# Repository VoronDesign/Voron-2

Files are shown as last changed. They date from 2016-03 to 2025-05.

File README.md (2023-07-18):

# Voron 2.4
**[CLICK HERE TO DOWNLOAD](https://voron.zip/done/V2.zip)**

The above link includes the stealthburner toolhead files which are compatible with several of the printers in the Voron lineup. 
To keep things organized, StealthBurner’s files are maintained separately. 
the Stealthburner Repository can be browsed by clicking [HERE](https://github.com/VoronDesign/Voron-Stealthburner)

Image of Voron 2.4

The official release of the Voron 2.4 3d printer.  You can find the BOM in the configurator located at the [Voron Design]( http://vorondesign.com/voron2.4) website.

Voron Logo

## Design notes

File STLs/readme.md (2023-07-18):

you can download the entire STL folder by clicking [HERE](https://download-directory.github.io/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)

This printer uses the StealthBurner toolhead, which is compatible with several of the printers in the Voron lineup. 
To keep things organized, StealthBurner’s files are maintained separately. 
the Stealthburner STL's can be downloaded by clicking [HERE](https://download-directory.github.io/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)

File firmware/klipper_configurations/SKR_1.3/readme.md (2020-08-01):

<B>VORON V2.4 SKR 1.3 Config</B>

This config file is for using two BigTreeTech SKR 1.3 boards on the Voron V2.4. For additional reference material, please reference BigTreeTech's Github page:

https://github.com/bigtreetech/BIGTREETECH-SKR-V1.3/tree/master/BTT%20SKR%20V1.3

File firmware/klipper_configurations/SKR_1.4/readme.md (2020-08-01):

<B>VORON V2.4 SKR 1.4 Config</B>

This config file is for using two BigTreeTech SKR 1.4 boards on the Voron V2.4. For additional reference material, please reference BigTreeTech's Github page:

https://github.com/bigtreetech/BIGTREETECH-SKR-V1.3/tree/master/BTT%20SKR%20V1.4

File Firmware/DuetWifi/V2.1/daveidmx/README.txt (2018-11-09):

Hello, and welcome to my configuration!

If you're new here:

1) This configuration works for my printer. Don't assume it'll work for yours out-of-the-box. Know and understand things before running them blindly.

2) The Duet Getting Started wiki is your friend:
    https://duet3d.dozuki.com/c/Getting_Started
    https://duet3d.dozuki.com/Wiki/Step_by_step_guide

If you want to base your configuration off of mine, here are some files you'll want to edit right away:

*  All settings in config.g.
*  All other files as marked to *ADJUST*:
**  /macros/drive/*.g for drive current and physics
***  "fullcurrent" files are used for normal printing.
***  "downcurrent" files are used for slow homing moves to reduce the impact of crash damage.
     You can opt out of the "downcurrent" profiles by uncommenting a couple lines as descibed in those files.
**  /macros/filament/do_moves_for_*.g for bowden length
**  /macros/heating/toolhead_*.g for your tool heater parameters.
***  NOTE: If you add or rename the profile scripts, also update the script name inside the script itself. This is to support recovering the selection across reboots to make it easy to switch toolheads.
**  /macros/homing/scripts/probe_zlevel.g for the leveling probe points
**  /macros/homing/scripts/probe_x.g for the X dimension
**  /macros/homing/scripts/probe_y.g for the Y dimension
**  /macros/moveto/*.g based on your dimensions
**  /macros/retraction/*.g for your retraction settings
***  NOTE: If you add or rename the profile scripts, also update the script name inside the script itself. This is to support recovering the selection across reboots to make it easy to switch toolheads and retraction profiles.
**  /macros/zprobe/use_i*.g for your inductive probe pins
**  /macros/zprobe/use_m*.g for your mechanical switch pins, and to tune Z-height
***  NOTE: /macros/zprobe/use_mslow.g is the only place you need to tune your Z-height.

Bonus files for the test scripts:
**  /macros/testing/belting/scripts/xy_point_*.g based on your bed dimensions
**  /macros/testing/belting/scripts/z_movecycle_1.g for your Z dimension
**  /macros/drive/*_torture.g

Changes:

* Default probe connectors have changed. The inductive probe has been moved from E0 to Zprobe to free up E0 for a filament detector.
* Added bindings for filament sensors. (Disabled by default.)
* Added bindings for chamber fan (enabled by default) and chamber thermistor and lights (disbled by default).
* Changed drive parameters for V2.1.
* Changed some other default settings to better match spec.

* Fix some fan and temp bugs in the /macros/heating/preheat_*.g scripts.
* Fix filament sensor configuration. (It wasn't turned on!)
* Make toolhead heater and firmware retraction profile selections sticky across reboots to support changing toolheads.
* Add retraction profiles for Volcano.
* Increased motor default idle timeout to 24 hours.

* IMPORTANT: Changed origin coordinates to be at bed center.
* Move toolhead thermistor parameters to the heating/toolhead_* scripts, because they change when you swap toolheads.
* Turn off extruder in print_end.g
* Set the tool to standby temperature (via deselection) when pausing.
* Added a heatbreak thermistor setting.
* Add calibrate_mswitch.g script to help calibrate the mechanical Z offset.
* Add coarse_level.g script to level the gantry for when the default dive height is too small.

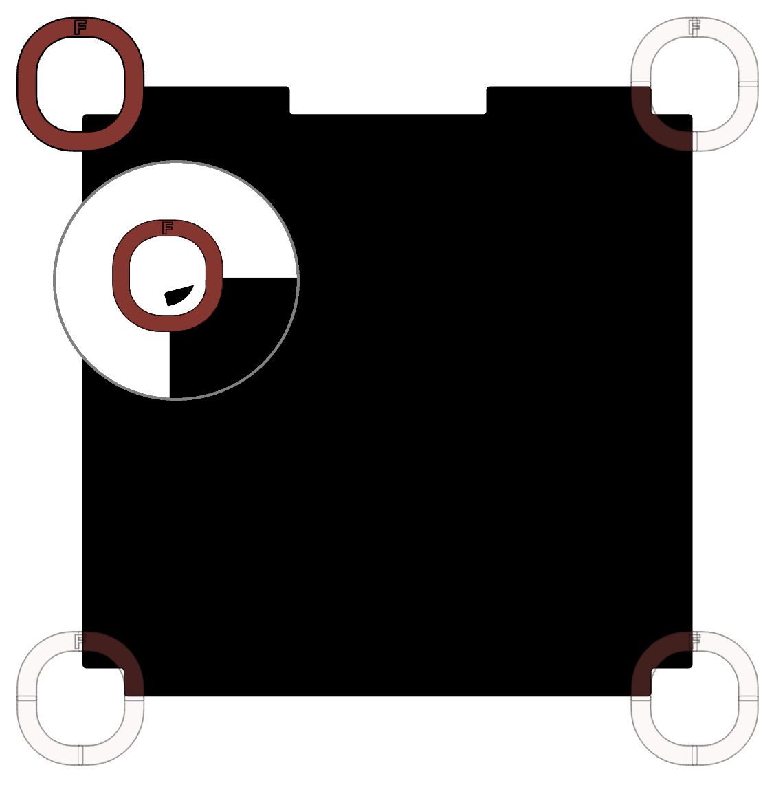
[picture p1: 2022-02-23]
STLs/Tools/bottom_panel_modification.png

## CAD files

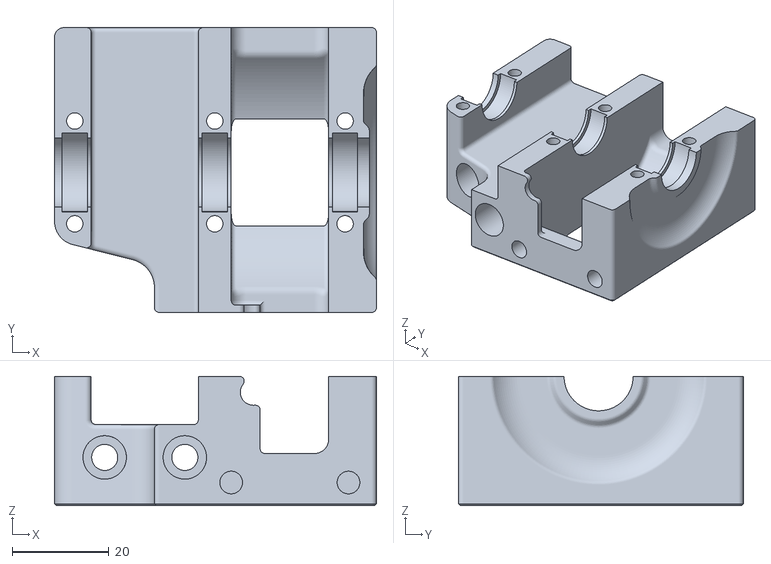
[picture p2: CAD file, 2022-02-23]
STLs/Z_Drive/z_drive_main_b_x2.stl
66.7 x 59.0 x 26.8

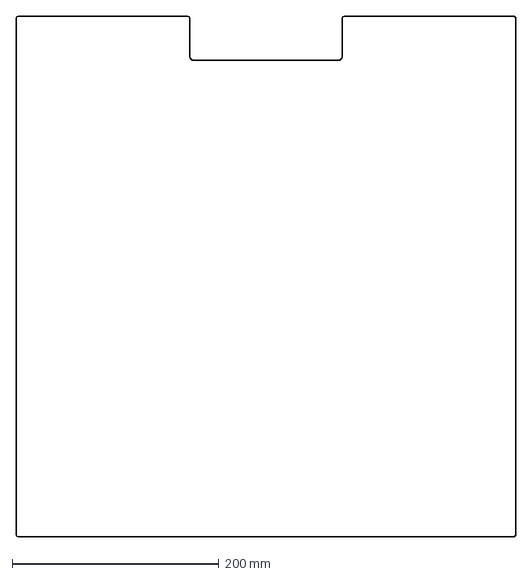
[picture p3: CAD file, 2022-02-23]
Drawing_DXFs/Panels/350_Back_Panel.DXF
483.0 x 503.0 mm

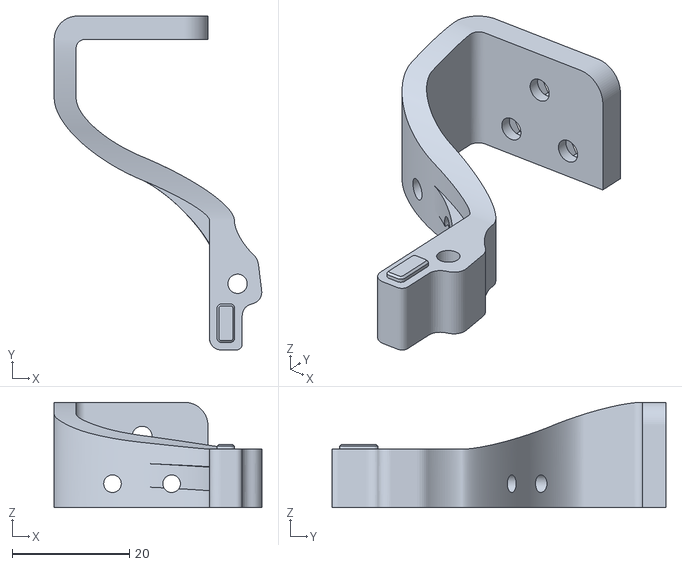
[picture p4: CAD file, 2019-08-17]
mods/warriorofwire/openbuilds_drag_chain_2.1/x_carriage_dragchain_anchorpoint.stl
35.4 x 57.0 x 18.0

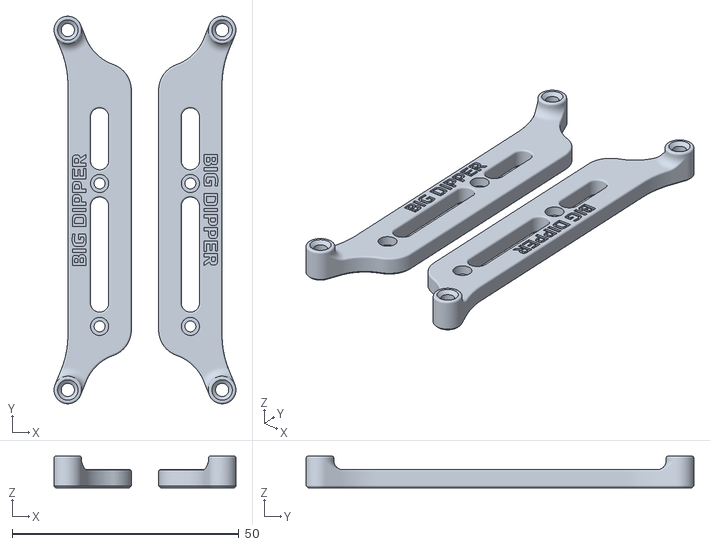
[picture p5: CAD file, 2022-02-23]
STLs/Electronics_Bay/Controller_Mounts/BIGDIPPER_bracket_set.stl
40.1 x 85.4 x 7.00

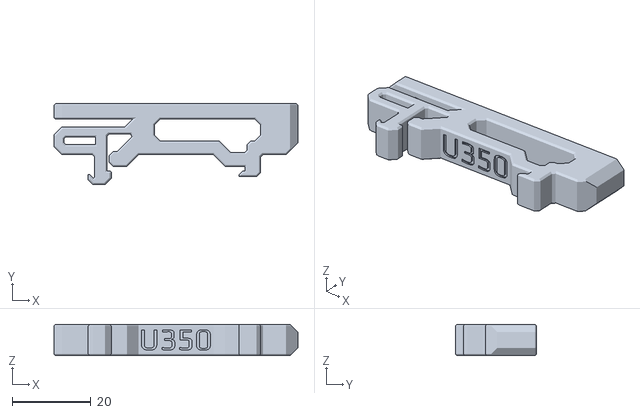
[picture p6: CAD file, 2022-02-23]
STLs/Electronics_Bay/Other_PS_Mounts/UHP_350_Mount_x2.stl
62.0 x 20.6 x 8.00

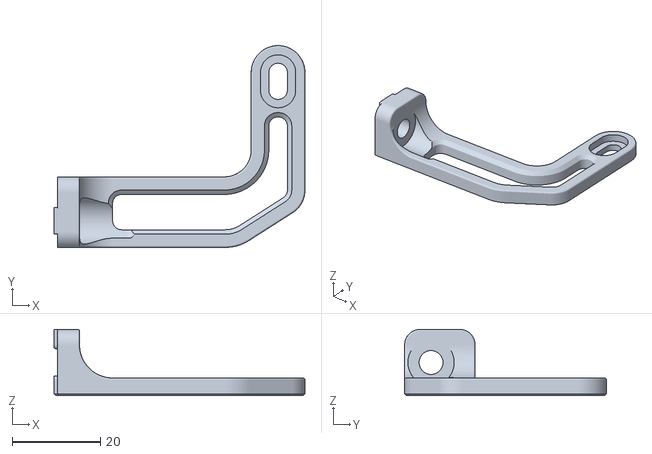
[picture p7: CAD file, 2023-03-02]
STLs/Electronics_Bay/PSU_stabilizer_50mm.stl
56.9 x 45.7 x 15.0

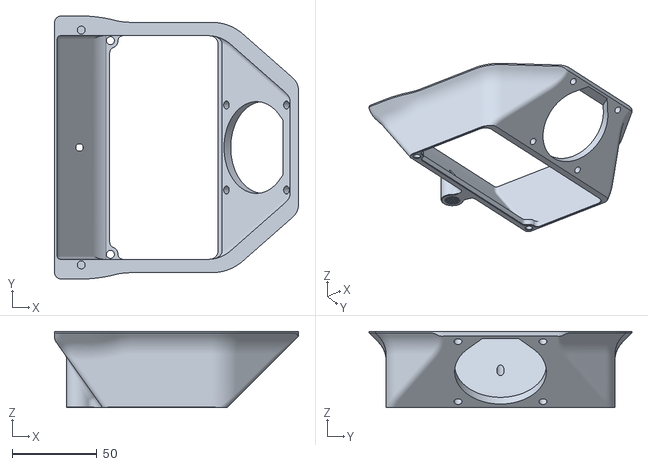
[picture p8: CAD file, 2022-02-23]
STLs/Exhaust_Filter/exhaust_filter_housing.stl
143.7 x 154.8 x 45.0

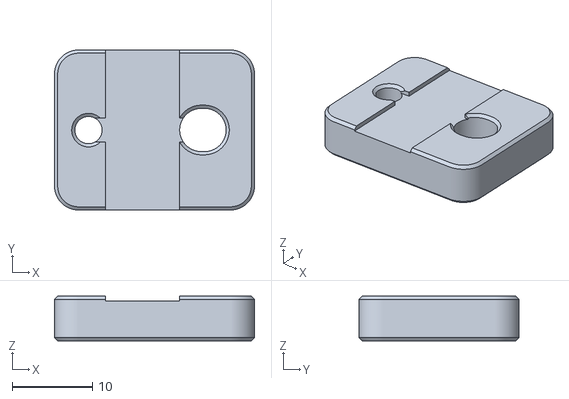
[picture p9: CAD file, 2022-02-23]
STLs/Gantry/[a]_z_belt_clip_lower_x4.stl
25.0 x 20.0 x 5.60

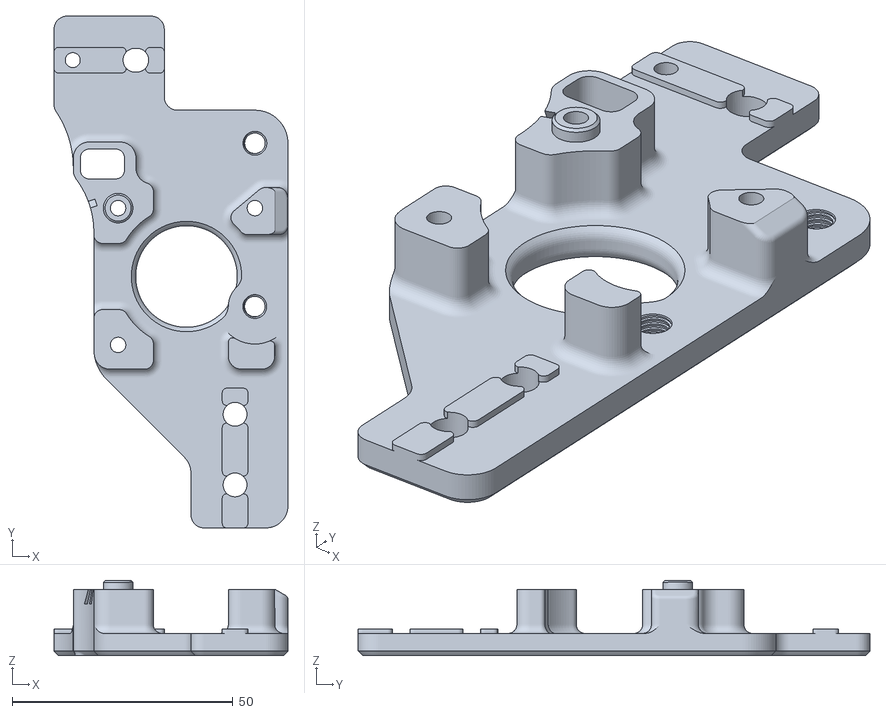
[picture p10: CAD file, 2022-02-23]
STLs/Gantry/AB_Drive_Units/b_drive_frame_lower.stl
53.0 x 116.0 x 17.0

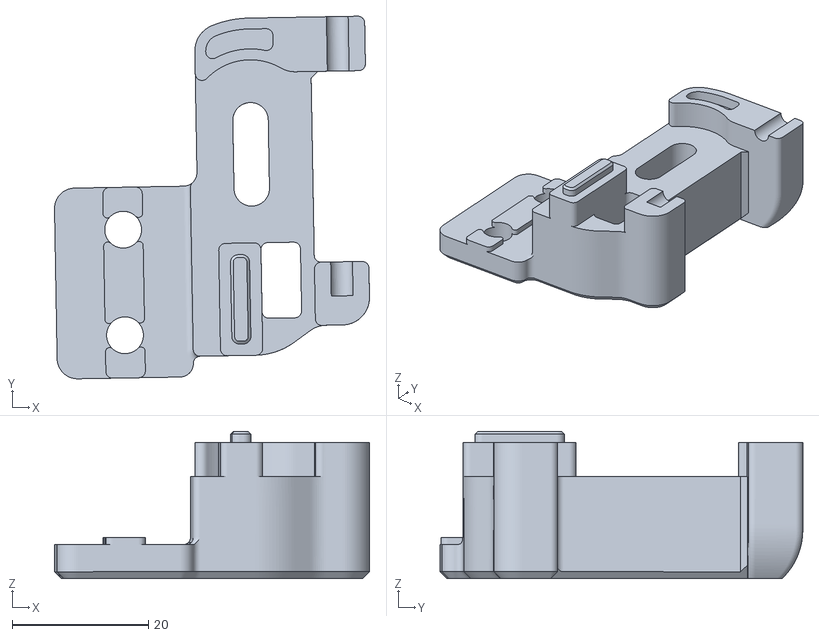
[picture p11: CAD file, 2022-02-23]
STLs/Gantry/Front_Idlers/front_idler_left_upper.stl
46.2 x 53.2 x 21.6

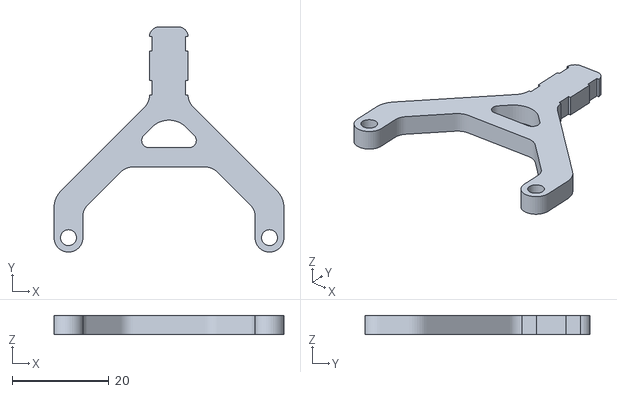
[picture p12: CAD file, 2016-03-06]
STLs/Gantry/X Carriage/Harness Anchor.stl
47.6 x 46.6 x 4.00

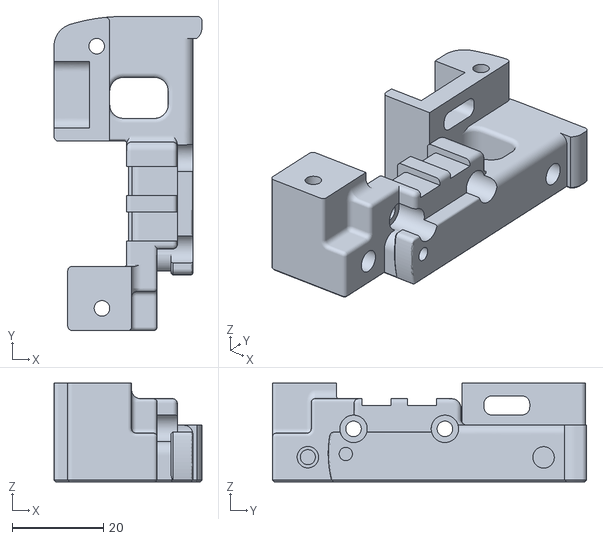
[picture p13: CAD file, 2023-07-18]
STLs/Gantry/X_Axis/X_Carriage/x_frame_V2TR_MGN12_left.stl
32.4 x 68.8 x 21.6

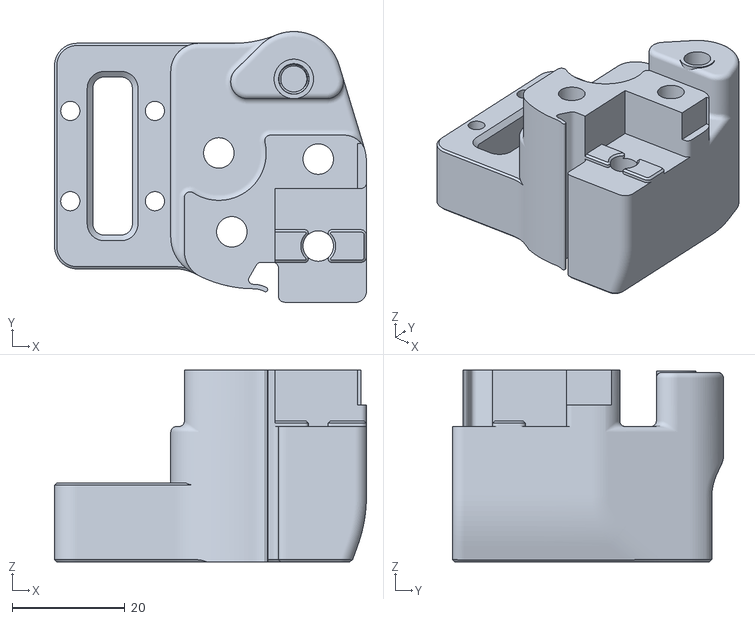
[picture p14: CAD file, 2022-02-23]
STLs/Gantry/X_Axis/XY_Joints/xy_joint_right_lower_MGN12.stl
55.3 x 48.0 x 34.0

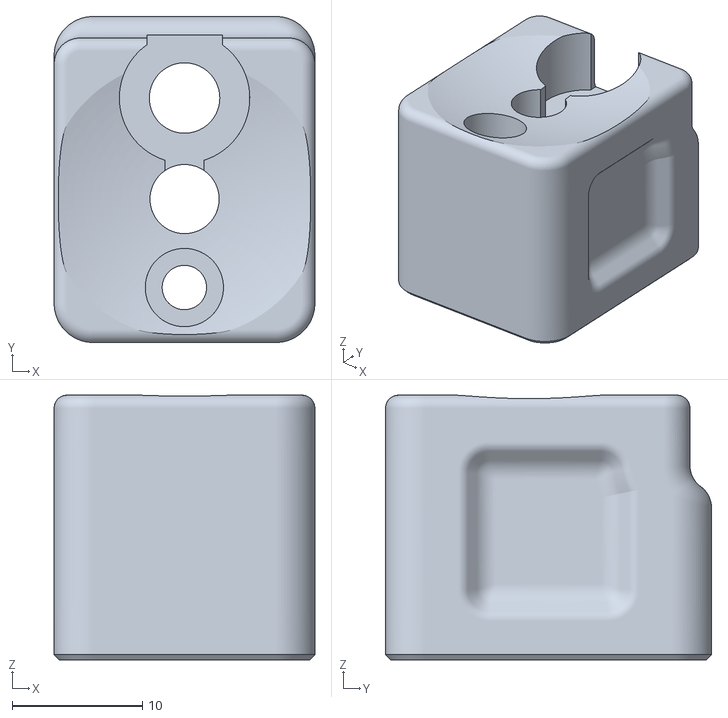
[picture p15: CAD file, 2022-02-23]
STLs/Gantry/Z_Joints/z_joint_upper_x4.stl
20.0 x 25.0 x 20.3

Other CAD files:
STLs/Z_Drive/z_drive_main_a_x2.stl
STLs/Panel_Mounting/Front_Doors/handle_a_x2.stl
STLs/Panel_Mounting/z_belt_cover_b_x2.stl
STLs/Skirts/250/rear_center_skirt_250.stl
Drawing_DXFs/Build_Plate/MIC6_Bed_V2_250.step
Drawing_DXFs/Build_Plate/MIC6_Bed_V2_300.step
Drawing_DXFs/Build_Plate/MIC6_Bed_V2_350.step
Drawing_DXFs/Build_Plate/VORON_Design_-_2.4Build_Plate_250mm.dxf
Drawing_DXFs/Build_Plate/VORON_Design_-_2.4Build_Plate_300mm.dxf
Drawing_DXFs/Build_Plate/VORON_Design_-_2.4Build_Plate_350mm.dxf
Drawing_DXFs/Panels/250_Back_Panel.DXF
Drawing_DXFs/Panels/250_Bottom_Panel.dxf
Drawing_DXFs/Panels/250_Deck_Panel.dxf
Drawing_DXFs/Panels/300_Back_Panel.DXF
Drawing_DXFs/Panels/300_Bottom_Panel.dxf
Drawing_DXFs/Panels/300_Deck_Panel.dxf
Drawing_DXFs/Panels/350_Bottom_Panel.dxf
Drawing_DXFs/Panels/350_Deck_Panel.dxf
STLs/Electronics_Bay/Controller_Mounts/BTT_MOT_EXP_bracket.stl
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

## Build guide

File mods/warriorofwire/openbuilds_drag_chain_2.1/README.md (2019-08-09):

# Off The Shelf Drag Chains for 2.1
Note: Tested with 300mm 2.1 build only.

## Why
* Drag chains with a snap open side are a joy to work on.
* It looks awesome.
* Looming up wires makes them harder to access.
* I hate tape chains.

## BOM
* Some M3 screws
* A few M5 screws that are a couple millimeters longer than the M5's on the gantry.  You'll figure it out.
* [3x Openbuilds 10x15mm 18mm radius Drag Chains](https://openbuildspartstore.com/drag-chain-cable-carrier/)
* All these stls

## STLs
File | Note
---- | ----
x_carriage_frame_right_remodeled | Parametrically driven remodel of the right toolhead without the wire tray.  The through-screws are modeled like the original stl, but they seem pretty tight from my printer.  YMMV, you might need a tap or just start working out more.
x_carriage_dragchain_anchorpoint | You screw your drag chain's floppy end to this side.
x_carriage_wire_cover | Cosmetic wire wrangler interfacing the drag chain to the X carriage.  Mounts with a short M3 screw.
xy_drag_chain_bridge | You screw your drag chain's floppy end to this side.  Wires go through it and up into the Y chain.
a_corner_wire_guide | Covers your wires around the A corner.  Keeps them from chafing against the rail and frame, while keeping them tidily away from the belt.  Also, you screw your drag chain's floppy end to this side.
lower_drag_chain_mount | Mounts to the rear lower frame.  You'll need to cut an L shaped slot into your bottom panel.  Also a great spot to run your bed and heater wires down through.  Move this on the rail until you get a little tension on your Z chain.  That'll keep it tight and it will look awesome.

## Known Issues
* I haven't accounted for the toolhead doors yet.
* X carriage screws are a little tight.  Probably "won't fix."
* A corner guide could be a little wider in critical places without interfering mechanically with the printer.  All my wires fit, but yours might not.

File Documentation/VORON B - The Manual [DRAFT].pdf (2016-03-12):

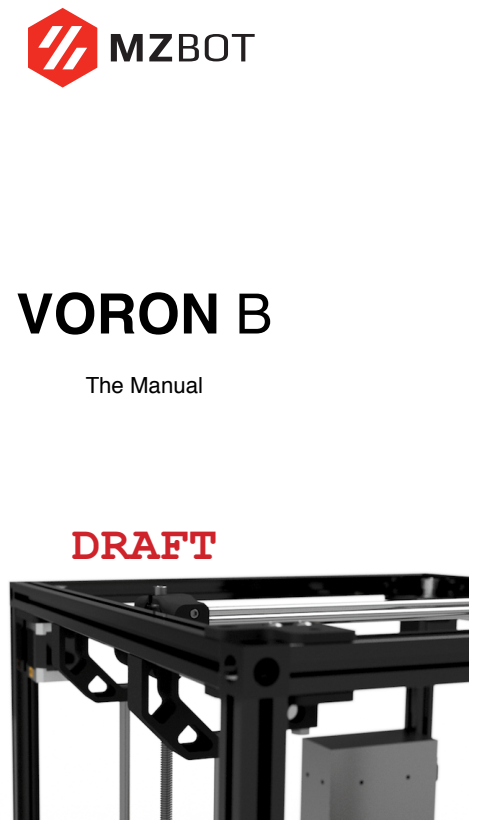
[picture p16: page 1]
VORON B; The Manual; DRAFT

## PRINTING PARTS

### Material

For majority of the parts on the printer, I recommend using ABS plastic (Black if you really want to replicate the look). Electronics enclosures can be printed with PLA as they don’t really have handle loads of high temperatures.

### Nozzle size

With exception of the X Carriage components, everything is deigned to be printed with a 0.6mm nozzle. You can use a smaller nozzle, of course, but be warned that some of the parts will take a significant time to print, and won’t be as strong.

### Print settings

In my experience the minimum settings to produce mechanically sound parts are:
- Layer height 50% of the nozzle width
- 5 layers for top and bottom
- 3 shells
- 40% infill (grid or honeycomb work equally well)

## TOOLS

Although no specialty instruments are requires, you will need some basic tools to build this bot. If you’ve built a RapRap before, you already have almost everything you need.

- Set of metric hex keys (I highly recommend ball-end ones)
- Set of metric drill bits (for cleaning out holes and making mount points in the bed)
- Drill
- Small knife
- Torx T25 driver
- Phillips screwdriver (#1)
- Soldering iron
- Pliers
- Wire cutters
- Ruler

Optional tools (they make the process less painful)
- Dupont connector crimpers (I highly recommend Engineer PA-09)

## SECTION1 : FRAME

Items required:

- 370mm 2020 Aluminum extrusions
- Cube Corner Connectors
- Self Tapping Torx Screws
- T Slot Nuts (M5)

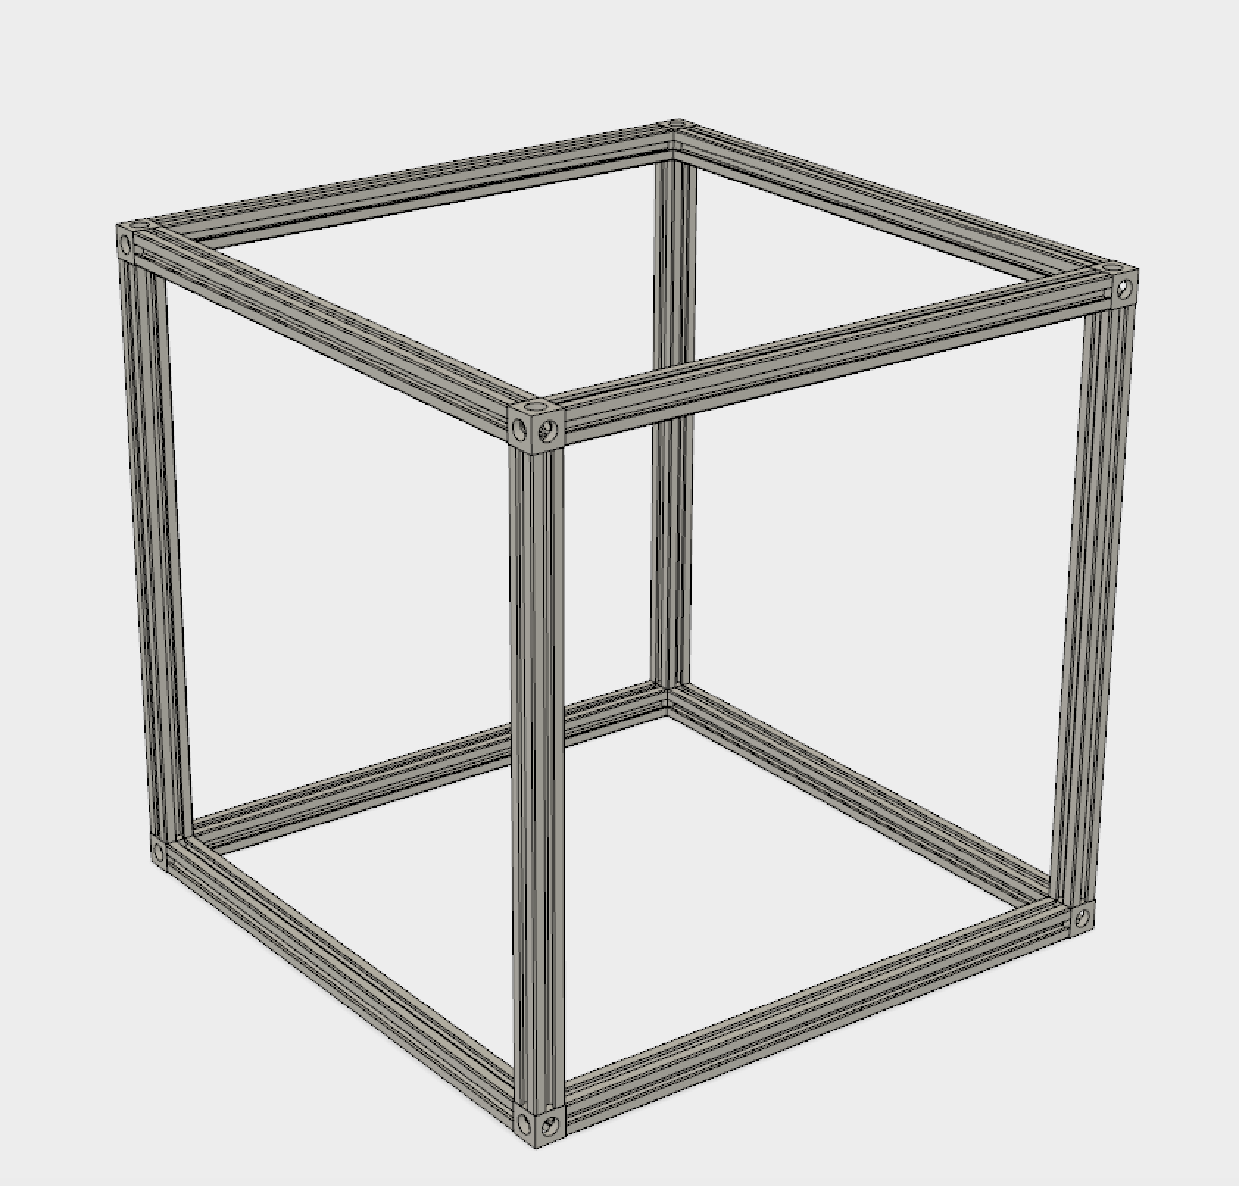
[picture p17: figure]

We’ll be building 2 squares and joining them together. Each length of 2020 extrusion needs to have the T nuts inserted during indicated step as they will be sealed inside the structure afterwards. For the purpose of preserving sanity let’s label these as follows:

TR | Top Right
TL | Top Left
TF | Top Front
TB | Top Back

Bottom flame pieces are labeled in a similar way.

Verticals are labeled as follows:

FR | Front Right
FL | Front Left
RR Rear Right (to avoid confusion with Bottom Right) RL Rear Left

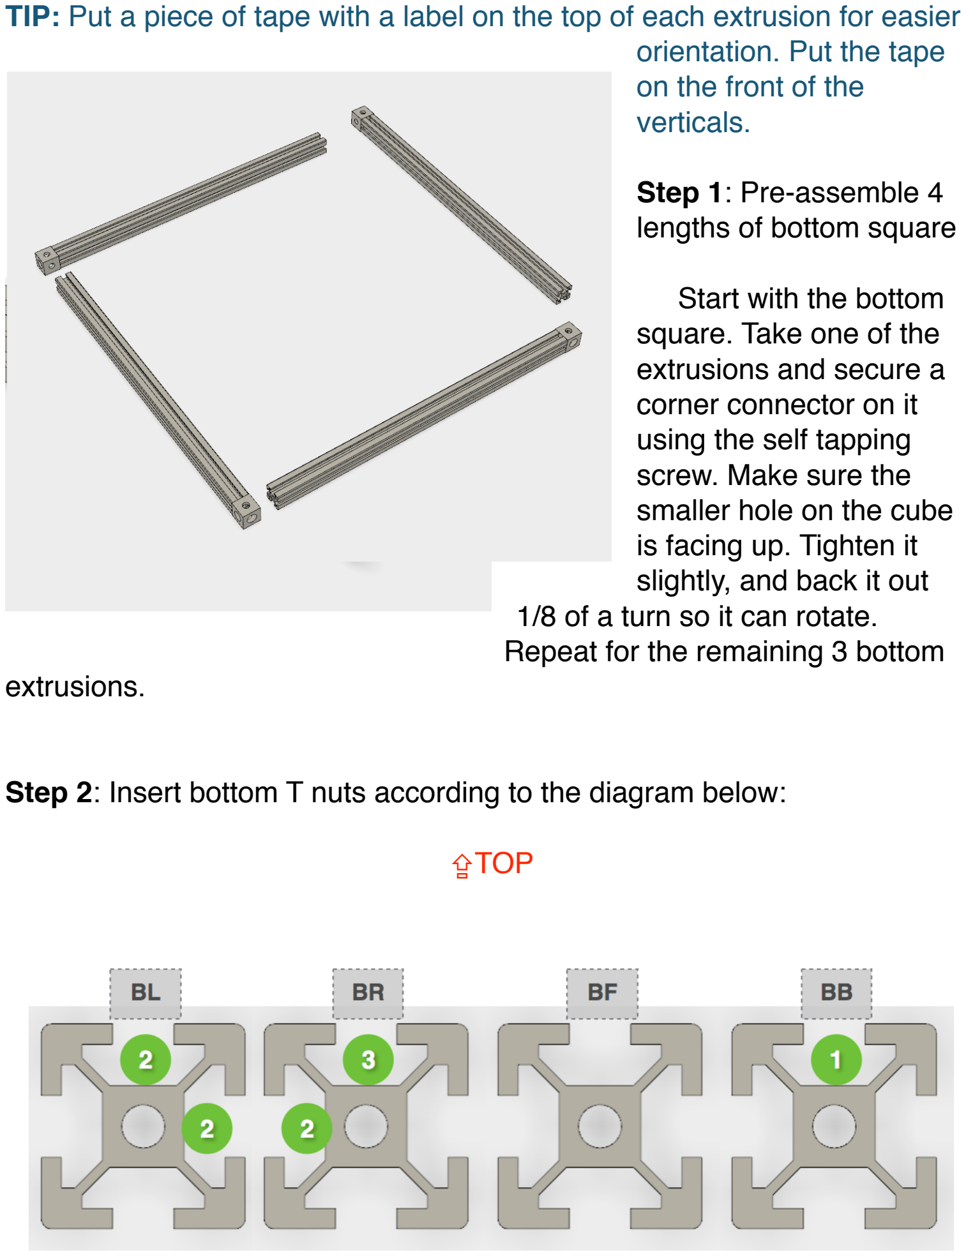
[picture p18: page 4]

TIP: Put a piece of tape with a label on the top of each extrusion for easier orientation. Put the tape
on the front of the
verticals.
Step 1: Pre-assemble 4
lengths of bottom square

Start with the bottom
square. Take one of the
extrusions and secure a
corner connector on it
using the self tapping
screw. Make sure the
smaller hole on the cube
is facing up. Tighten it
slightly, and back it out
1/8 of a turn so it can rotate. Repeat for the remaining 3 bottom extrusions.
Step 2: Insert bottom T nuts according to the diagram below:

⇪TOP

Step 3: Join the 4 pieces into a square.

You’ll have to apply some force to get the screws to go in all the way. It’s a really tight fit inside the cube. Don’t worry, it’ll connect. Just go slow and make sure the screws are all the way in. You can then back them out 1/8 of a turn. Make sure you are applying ample thrust so the torx drive doesn’t slip.

Find a flat surface, and applying pressure to the top of it, tighten all of the screws. This will ensure the square is flat (or flat enough).

Step 4: Repeat Step 1 for the top 4 extrusions, making sure the smaller holes on the cubes are facing the bottom this time.
Then insert the T nuts according to the diagram below:

⇪TOP

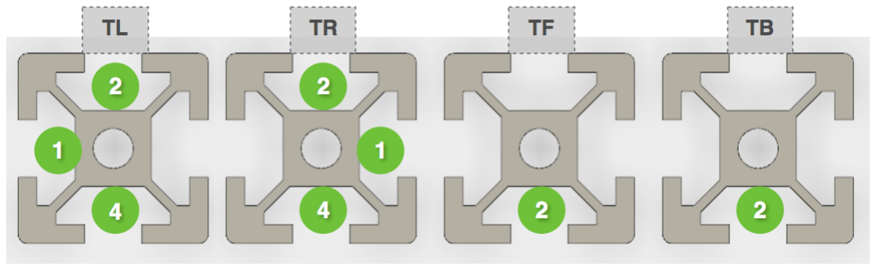
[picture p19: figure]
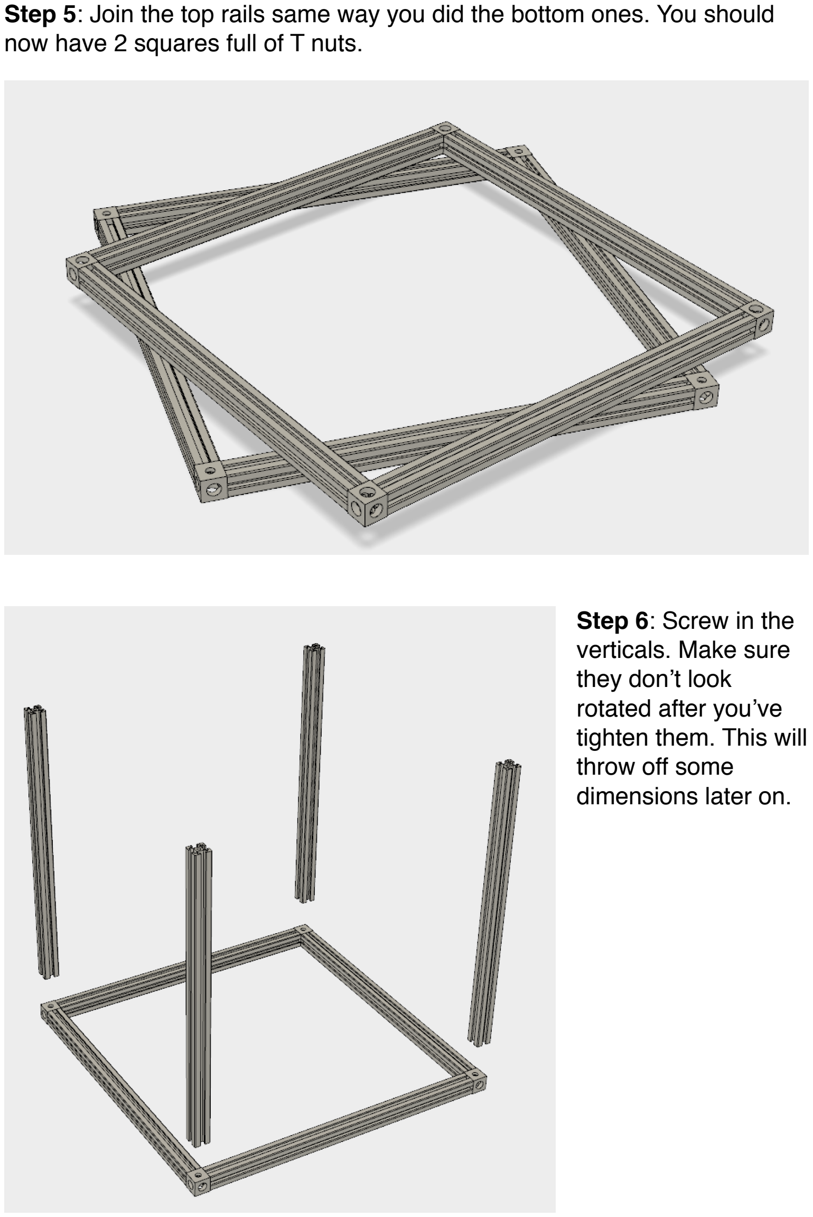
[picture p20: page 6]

Step 5: Join the top rails same way you did the bottom ones. You should now have 2 squares full of T nuts.
Step 6: Screw in the
verticals. Make sure
they don’t look
rotated after you’ve
tighten them. This will
throw off some
dimensions later on.

Step 7: Insert the remaining T nuts into the verticals:

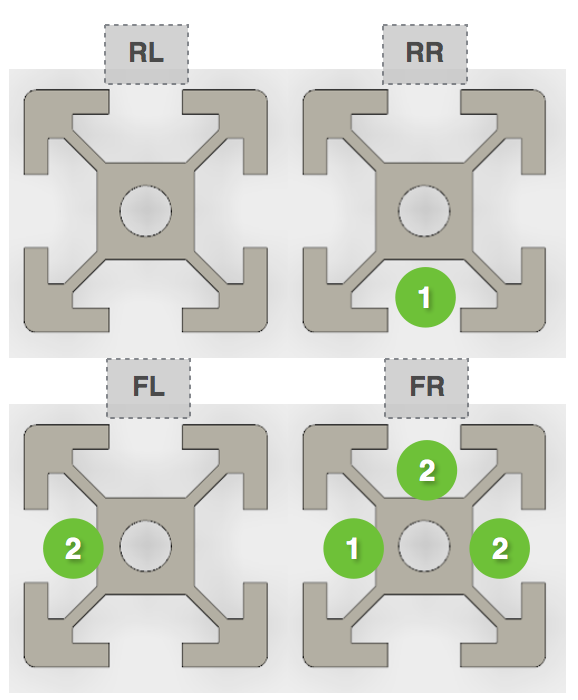
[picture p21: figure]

↓FRONT

Step 8: Attach the top square to the verticals. Tighten everything and check the diagonals with a ruler. The diagonals need to be as close to 524mm as possible. If they are off too much, you’ll need to loosen some screws and re-tighten them on
a flat surface. If
they are still
tweaked, you can
gently guide them
into true with some
strategically
applied pressure.
Having a square
frame will save
you a lot of
calibration
headaches in the
future.

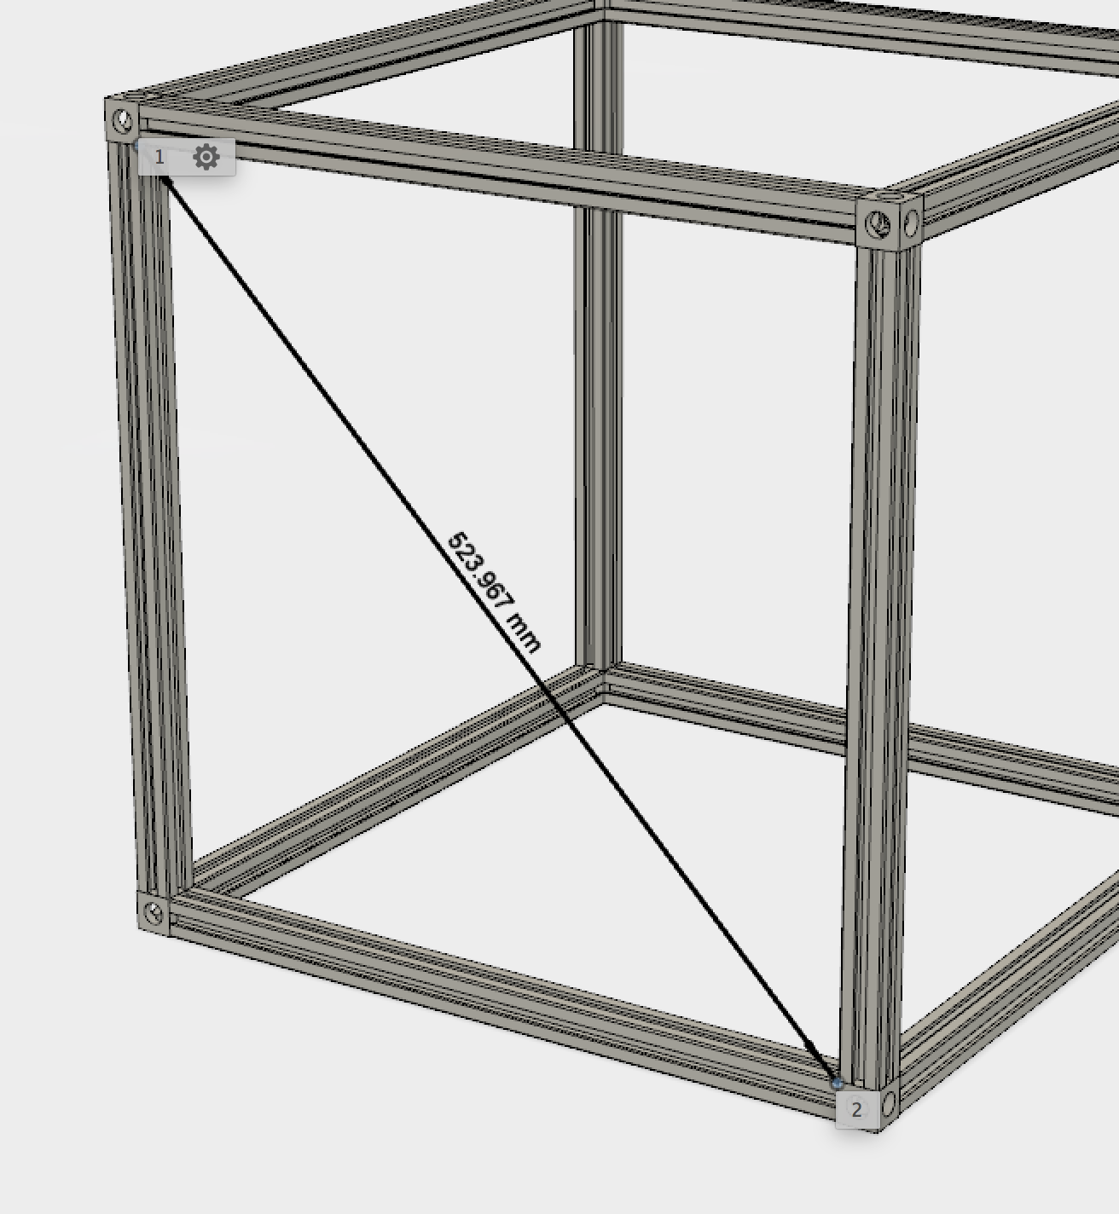
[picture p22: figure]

Congrats! You now have a solid frame to build your printer on. On to the more fun bits.

## SECTION2 : GANTRY

### A/B Motor Mounts

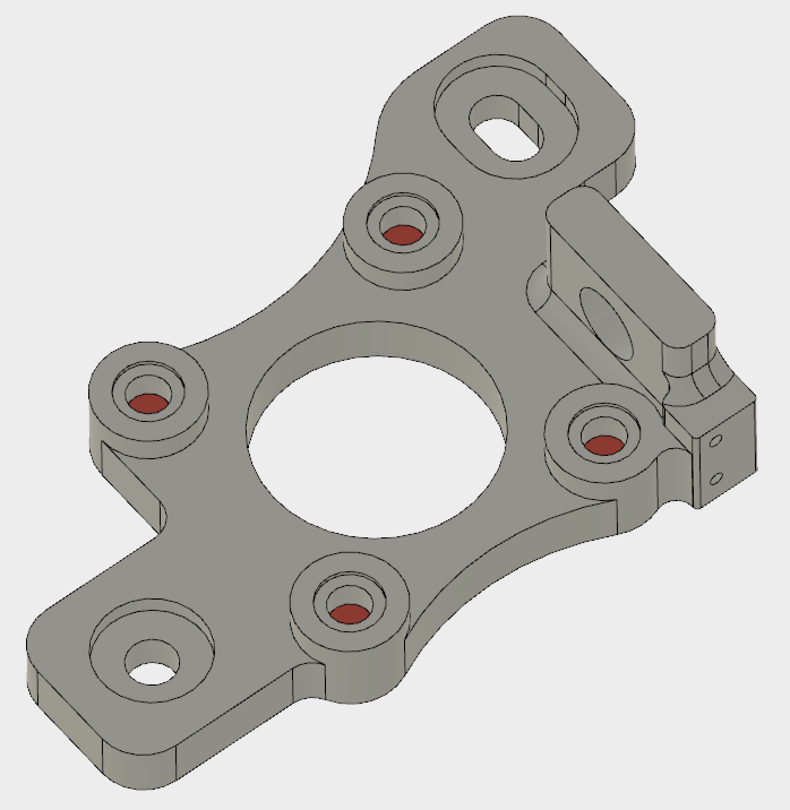
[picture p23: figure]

Step 1: First, a little cleanup. You’ll need to remove some bridging support material from the motor mount holes (colored red in the illustration). 4mm drill bit does the job quite well, but a small knife will do the trick.

Now is a good time to check if the 8mm shaft fits into its mount point. It should be a snug fit, but go in with only a little pressure. If you feel you have to hammer it in, stop and clean out the hole a little.

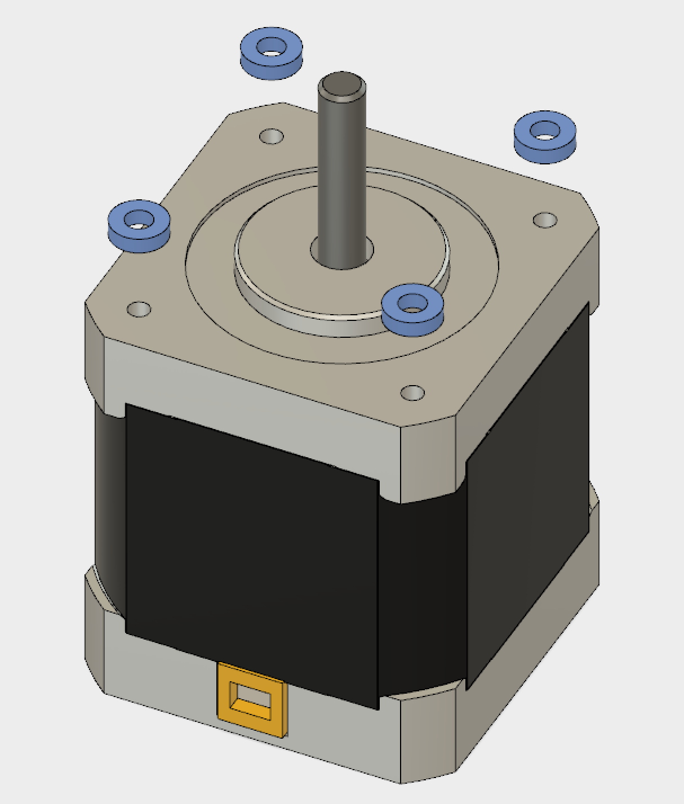
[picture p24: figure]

Step 2: Place the NEMA17 stepper on a level surface, and place 4 silicone washers on top of it, aligning them with the holes on the stepper. The washers are a little sticky and should stay in place.

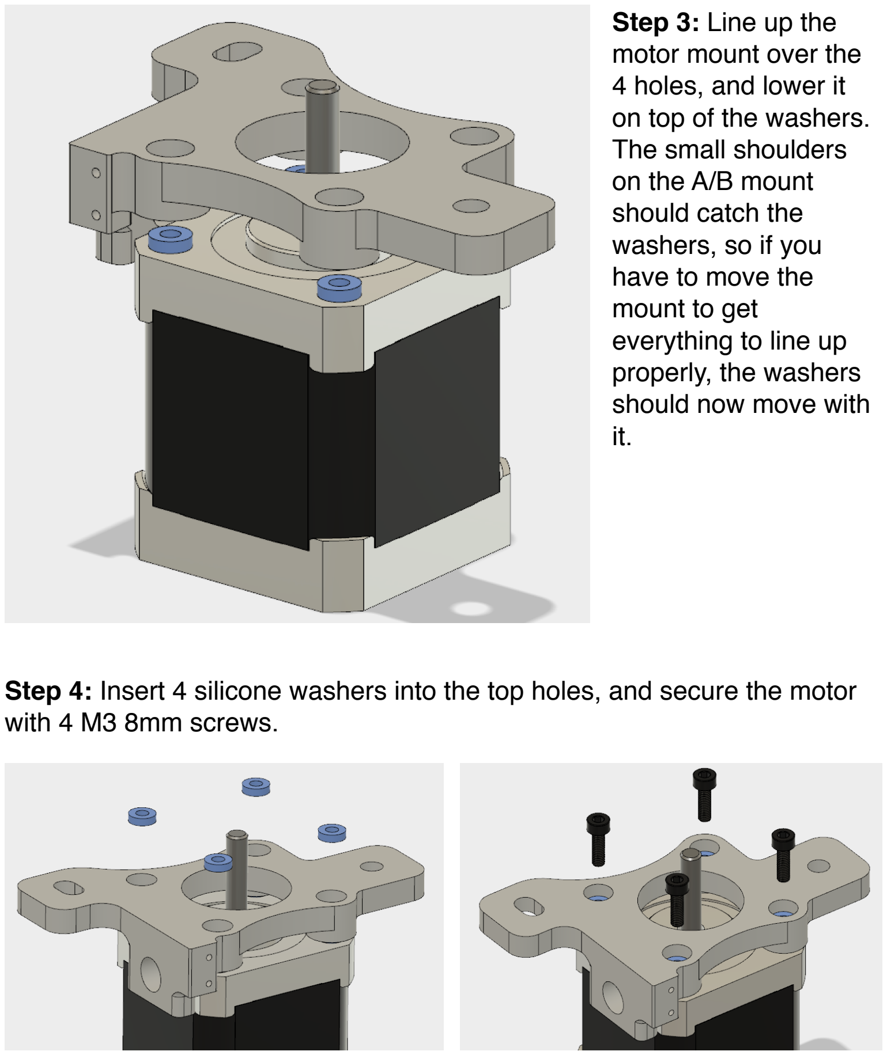
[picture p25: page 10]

Step 3: Line up the
motor mount over the
4 holes, and lower it
on top of the washers.
The small shoulders
on the A/B mount
should catch the
washers, so if you
have to move the
mount to get
everything to line up
properly, the washers
should now move with
it.
Step 4: Insert 4 silicone washers into the top holes, and secure the motor with 4 M3 8mm screws.

Tighten the screws until there’s about 0.5mm gap between mount and the motor. You should still be able to see the blue washers between the stepper and the mount (as in the picture below). We’re trying to stiffen the joint, while preventing the stepper from making contact.

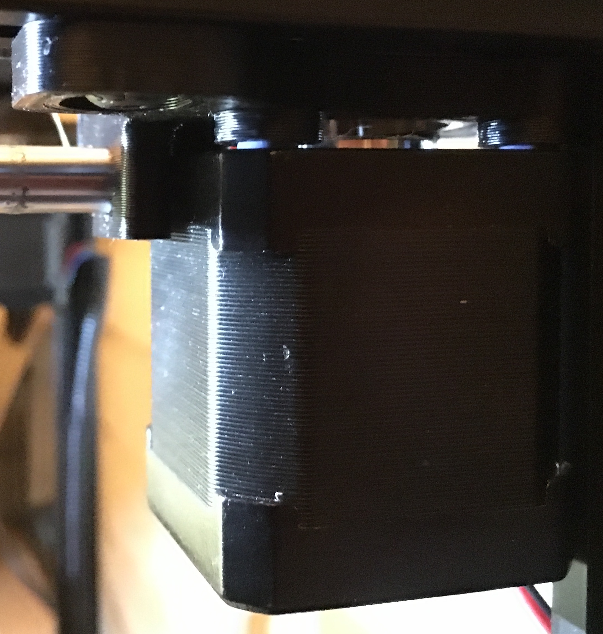
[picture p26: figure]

Repeat this process for the other motor mount.

### A/B Idler

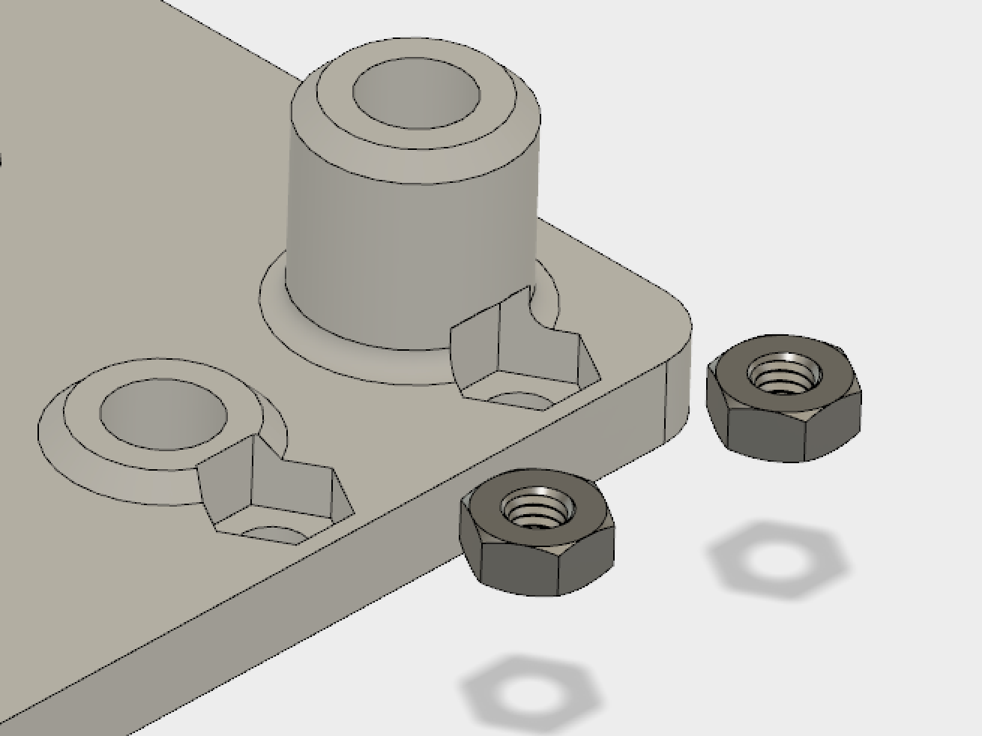
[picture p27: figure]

Step 1: Insert M3 hex nuts into the lower idler plate

WARNING: Do not drill out
the bottom 2 idler posts. We need them to be snug so the screws have something to
form threads in.

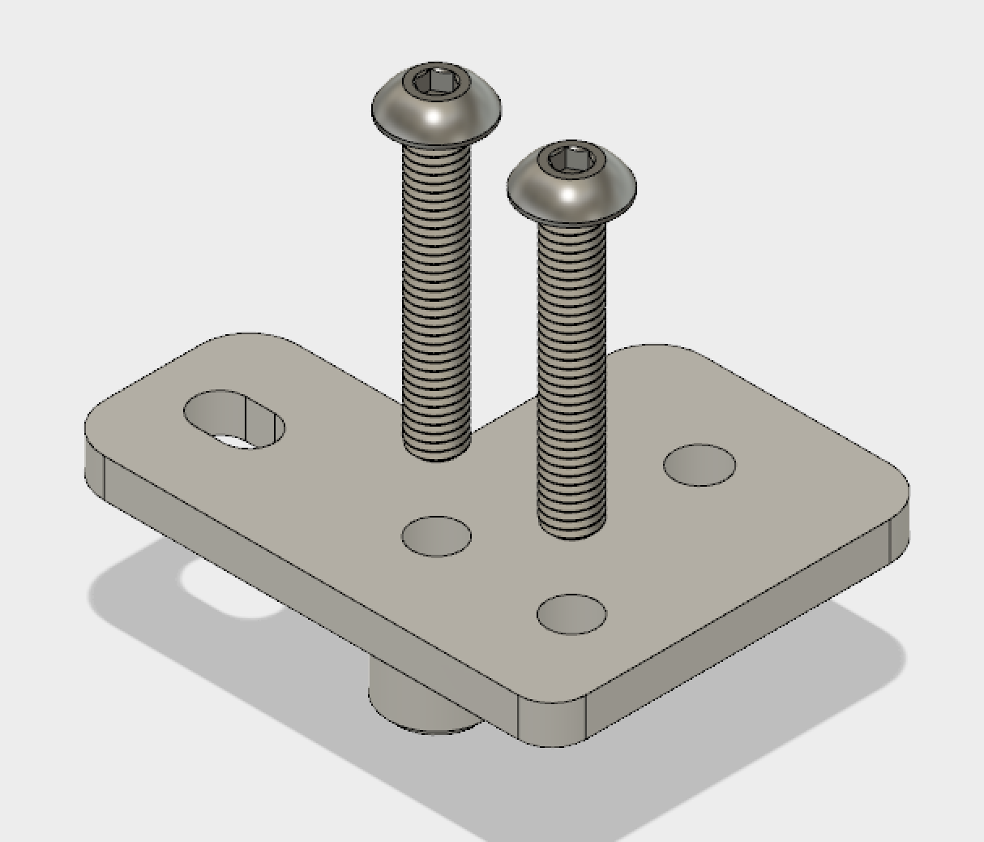
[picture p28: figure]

Step 2: Screw the 2 M5
30mm screws into the upper idler plate, and give them a few twists so they break the threads they just formed in the plastic. These holes
have intentionally tight
tolerances.

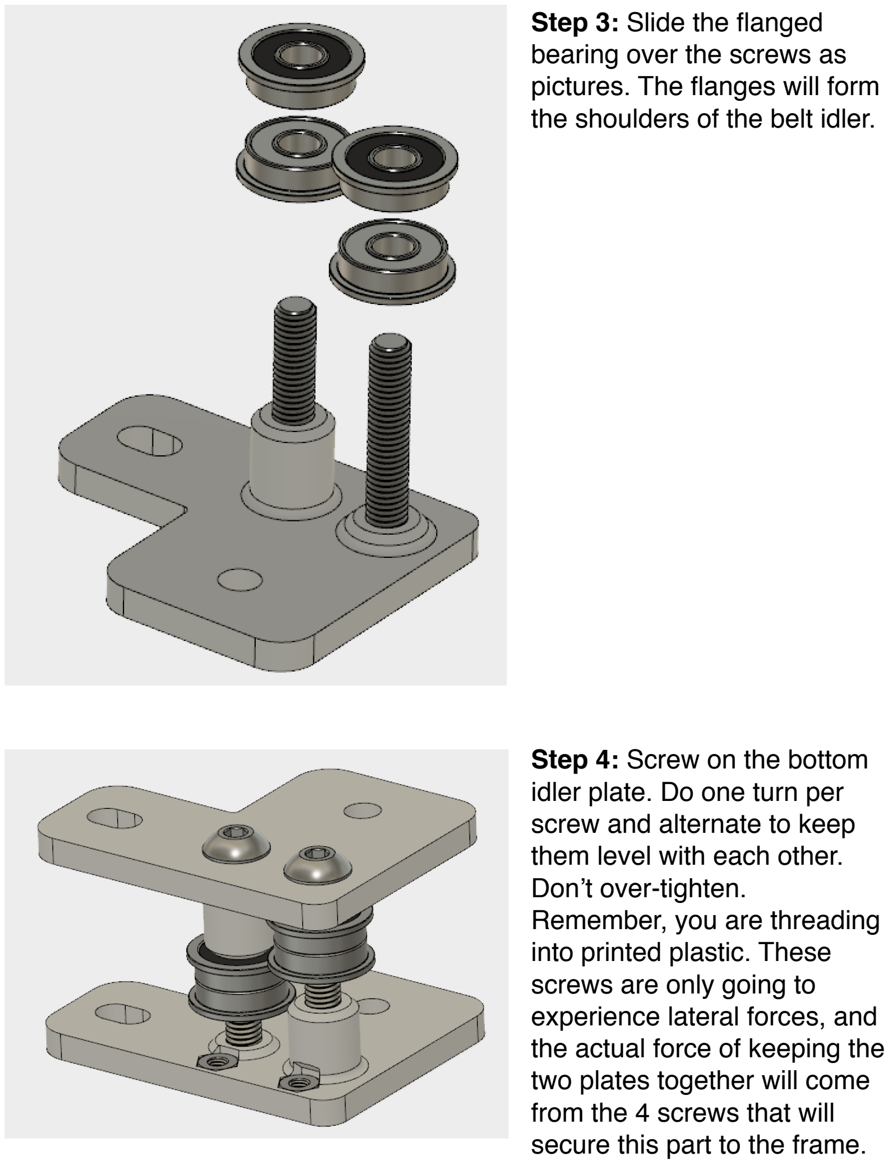
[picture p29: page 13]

Step 3: Slide the flanged
bearing over the screws as pictures. The flanges will form the shoulders of the belt idler.
Step 4: Screw on the bottom idler plate. Do one turn per screw and alternate to keep them level with each other. Don’t over-tighten.
Remember, you are threading into printed plastic. These screws are only going to
experience lateral forces, and the actual force of keeping the two plates together will come from the 4 screws that will secure this part to the frame.

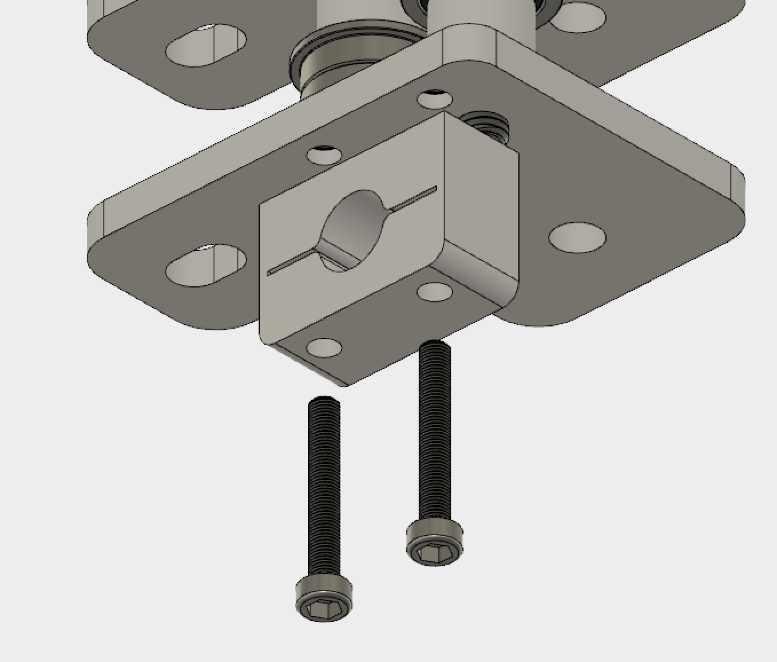
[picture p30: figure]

Step 5: Using 2 M3 20mm
screws, secure the Y shaft retainer into the lower idler plate. We’re not tightening these yet, just keeping them in place for later.

Repeat for the other idler.

Woo! You now have a Y axis!

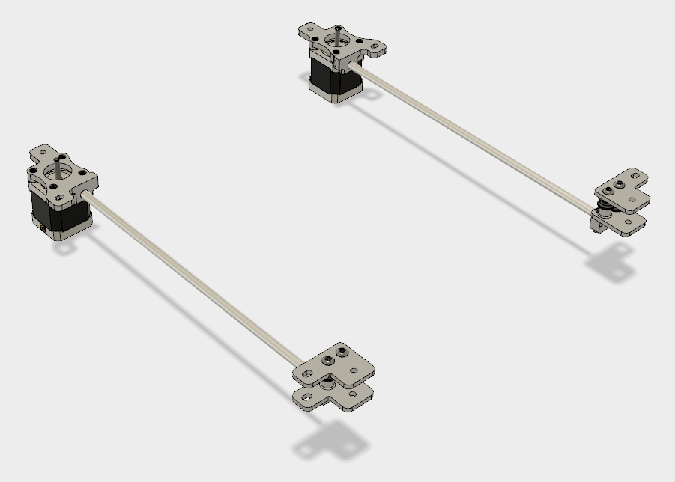
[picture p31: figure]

After you’re done
admiring your handy
work, remove the Y
shafts. They will be
installed after the
components are
bolted into the frame.

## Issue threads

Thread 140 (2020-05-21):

Belt misalignment in F3D assembly v2.4

eholley, 2020-05-21:
Yikes! Belt A is offset a bit from the idler pulley. Left and right sides show a similar issue. I was planning on 3D printing my belt, so good thing I caught this! ;)

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

FHeilmann, 2020-12-09:
The belt CAD should not be used for anything other than a guide on where the belt is supposed to go. The belt in the CAD as it is is a finicky beast so we're not going to fix this minor issue at this time.

Bests,
-Florian

Closed 2020-12-09.

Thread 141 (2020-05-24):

Parts are loose in v2.4

yhaiovyi, 2020-05-24:
There's 0.1 mm expansion compensation put directly into cad files. Now all parts I have already printed on a calibrated machine go into trash. So my proposal would be to add compensation as a variable, or just don't compensated at all, because that's not the right way to solve printing issues that some users might experience. CAD sizes should be precise.

yhaiovyi, 2020-05-24:
A few examples:
- Bondtech axial bearing is 8mm. The corresponding hole size in CAD is 8.2mm.
- Z drive bearing is 20mm. The corresponding arcs sizes is 20.3mm!
Moreover it seems like compensation is not consistent, and meant to fix issues with some particular printer/filament.

yhaiovyi, 2020-05-24:
Now my own experience.  I never worked with materials that would give that bad expansion. the biggest expansion compensation I've ever done was 0.09mm, and most certainly not 0.15mm. 0.15mm is severe over extrusion.

Maglin, 2020-06-21:
.2-.3mm is standard ABS compensation for ABS shrinkage.  Some parts are designed for a sliding fit and not a press fit that would end up breaking the part from the stresses.

You never said what material you are using but every functional part of the Voron 2 printer is designed for ABS.

Closing as this is as designed.

Closed 2020-06-21.

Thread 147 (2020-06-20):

Voron VFA's how to remove them (Vertical Fine Artifacts)?

homepods, 2020-06-20:
What are VFA's (Vertical Fine Artifacts)? They are fine vertical lines that appear on printed surfaces.

As for VFAs, one that is noticeable in every Voron 3D print, is some sort of Z banding, as the surface going up the bed, isnt perfectly straight and there is some sort of miss alignment of the extrusion.
I am comparing Voron (because of it's price point) to everything above other printer in terms of quality.

Now, please don't ignore this issue, let;s find a way to fix it through cooperation.

I am trying to understand why this happens. Is it caused by Z guide rails, or AB guide rails? or E guide rails? Is it by the belt tension or by stepper motors?

It is caused by pulleys or by the whole design because guide tolerances  are variable?

Who agrees to have small Z-banding and wants to remove it?

doowrednu, 2020-06-21:
I don't have any z-banding - so not sure what you mean

arch-xanin, 2020-06-21:
VFAs and z-banding are two different things.

I do not agree to have any z-banding, small or otherwise.

Tell us more about your voron and what you are seeing in your prints specifically please?

homepods, 2020-06-21:
2.4 it is not just me - I can see all pictures from voron showcase on discord to have layer miss-alignment going up the Z like Z-Banding.

Also Nero made a live-stream and his cube had also z-banding.
https://www.youtube.com/watch?v=bURkB-ecNbw&t=14037s

Guys from Poland Druk3D have Z-banding.
https://youtu.be/X2vB1MGsWLk?t=890

It appears that not just me, but every print has some sort of Z banding.

Is this a mechanical or electronic derived miss-alignment. What do you guys think? Where should I focus my correction mod to fix the problem.

I am trying to understand why this happens. Is it caused by Z guide rails, or AB guide rails? or E guide rails? Is it by the belt tension or by stepper motors?

It is caused by pulleys or by the whole design because guide tolerances are variable?

Maglin, 2020-06-21:
This is an effect of how 3D printed parts are made with FDM.  It's superficial and moving to a very low layer height resolution can make it seem to disappear.  This is a non-issue.  It's able to be seen in EVERY FDM print for any printer.

My analogy for this would be similar to "why is the block of steel so heavy?" or "how come every time I put fire on this dry wood it burns?".  You are extruding a circular cross-section and when you stack them you will have this effect.  Of course, you wouldn't see it on say SLA, SLS, MJF etc because it's a process that leads to actual flat walls.

doowrednu, 2020-06-21:
If people do not tune their printers that is down to them - I see 1,000's of trash prints on an ender to every 1 decent one - it is the same for any 3d printer

homepods, 2020-06-21:
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

Not every 3D printer has this issue. Some 3d printers, like the cheap ender 3, creality or others in that category. Yes, if you tune them as @doowrednu  says, can increase their quality, meaning to change their extruder, tighten their v-slot rails, change the termistor, the MCU and so on.

So my question is where should I look to tune it. Anyone has achieved zero Z-banding on a Voron, can I see some examples so I can build my confidence, cuz at the moment I am confused!!

VoronDesign, 2020-06-21:
This discussion is going nowhere. Please do some basic modicum of research.

homepods, 2020-06-21:
are you going to hide the issue instead of being open to look for a fix! lol ... it's a problem and there has to be a solution! don't ignore it cuz it will come to you sooner or later.

doowrednu, 2020-06-21:
This issue tracker is for owners of the printer - when you have built one and tuned it please feel free to create an issue. If you want to continue to discuss hypothetical problems - please do it elsewhere.

Closed 2020-06-21.

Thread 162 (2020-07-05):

V2.4 Wrong M2 self tapping screw in BOM and wrong amount

lazymaniac, 2020-07-05:
Hey

In BOM I found M2x10 listed, but in instruction manual says about M2x8. M2x10 are too long for DIN mounts because they go all the way through.

lazymaniac, 2020-07-05:
Also the amount is incorrect. Instruction requires 16 screws (2 - z endstop, 4 - xy endstops, 2x2 - skr mounts, 6 - rpi) but in BOM - 10

avongil, 2022-01-10:
The mcmaster screws are too short to attach the microswitch reliably. The head is also way too big for that application if you want to lay them flat and solder the JST direct. I had to source other ones that had a thinner head and longer body for all the end stops.   The din rails where ground flush.

avongil, 2022-01-10:
The Digikey switches have holes that are a tiny bit larger than 2mm, so it would not hurt to keep the McMaster linked screw at 1.91mm. The linked McMaster screw is an M1.91 https://www.mcmaster.com/99397A267/   - these screws I was not a fan of. Note how big the head is - 4mm.

 I propose either one of these - they are a much better fit for the switches and will work everywhere:

 https://www.mcmaster.com/99461A620/
 https://www.mcmaster.com/96001A127/

Current screws in the BOM from McMaster (head diameter too large):
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

DigiKey microswitches on the BOM have holes that are 0.081" in diameter - 2.06mm.

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

avongil, 2022-01-15:
Confirmed the mcmaster part: https://www.mcmaster.com/99461A620/
Is a way better fit, and also easier to cut if you have to although it looks like the new style din connectors are made for it. Great job Steve!  Gorgeous and well labeled parts.
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

I did not want to bust off the flap, but this fits way nicer than the official linked mcmaster part in the microswitch.  3.5 fully engaged threads.
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

Closed 2022-02-23.

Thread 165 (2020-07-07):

[V2.4] Spool holder too short to fit Amazon Basics PLA spools

msharp58, 2020-07-07:
Current spool depth for Amazon Basics filament is 76mm.  The spool holder in its current state supports a maximum depth of about 73mm.  This is easily fixed by scaling along the x axis during print, but it might be worth lengthening it in the CAD and STL files.

Lefuneste83, 2020-08-12:
You are correct. There is a User Mod for a wider spool holder that I have printed as my 3DJake spools wouldn't fit on the regular spool holder.
https://github.com/VoronDesign/VoronUsers/tree/master/printer_mods/raymondh/LargeSpoolHolders

insurgus, 2020-09-25:
Usermod recommended. Closing.

Closed 2020-09-25.

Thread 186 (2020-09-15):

2.4 BOM is short 3x M5x16 bolts

jrosen9, 2020-09-15:
I ran the configurator for a direct feed, 300mm with Misumi corner cubes.  The produced BOM stated I needed 11 M5x16 screws.  Following the manual, I have needed 14 of these of these screws

julianschill, 2020-11-29:
It is actually short on 4x M5x16. In the manual there are 2 on page 51, 4 on page 52, 4 on 54, and 1 for the spool holder. Then you need 4 for the bed and 16 for the frame for blind joints. That makes 31 for blind joints and 15 for corner cubes.

julianschill, 2021-05-28:
The BOM is indeed short of 4 M5x16. Here is an image of where the M5x16 are used:
![Uploading VORON2_v2.4_Assembly_v1.png…]()

cyrix2000, 2021-11-19:
Why is the BOM now showing just 11 M5x16 BHCS bolts?

Closed 2022-02-23.

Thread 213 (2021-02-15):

Door panels have no tolerance

julianschill, 2021-02-15:
When ordering everything to spec, the door have zero tolerance and don't close properly, especially when getting warm. They block each other in the middle and at the latches.

I would suggest to specify the doors 0.5mm smaller in both directions.

Alternatively the hinges and latches should account for that.

NameOfTheDragon, 2021-05-16:
Let's not be hasty, I like the snug fit. I didn't like it to begin with but it has grown on me. On my build the panels line up perfectly in the middle and its almost as if you have a single piece across the front. I find this desirable from the point of view of draft exclusion and keeping in the heat. It does take a little jiggle to get them to close like that but now that I'm used to it I'm OK with it.

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

There's always the option to trim them down a bit or sand with a sanding block, it's better to start with a tight fit and sand down than have too big a gap, although I suppose you do have some leeway at the hinges.

claytono, 2021-05-18:
I've had this problem also.  Both sets of door panels I've ordered from PrintedSolid have met spec, but had slight interference issues.  If they were 0.5mm smaller, then you could mount them on the hinges closer to the center if you prefer that, but with the current size, that's not an option.

stvptrsn, 2021-05-19:
Most cut to order shops specify a cut tolerance.  For instance this is the text from Tap Plastics "Cut to size orders are cut with table and CNC panel saws and have a cut tolerance of +/- .060”. Plastic sheets have a thickness tolerance of +/- 10% and can have thickness variations throughout the sheet. Cut to size items cannot be returned for a refund or exchange."  Accounting for this in CAD is not reasonable and you should expect to check your panels before install and adjust as necessary.

julianschill, 2021-05-19:
A solution could also be to design adjustable hinges, so you can move the doors around a few 0.1mm until it fits and compensate for the tolerances of the cutting.

claytono, 2021-05-19:
@stvptrsn I assumed this was more of a BOM than a CAD issue.  Are the BOM dimensions adjusted for that sort of thing?

stvptrsn, 2021-05-19:
> @stvptrsn I assumed this was more of a BOM than a CAD issue. Are the BOM dimensions adjusted for that sort of thing?

I don't think so.  But it's hard to compensate for what could be a 3mm swing based on advertised cut tolerances.

claytono, 2021-05-19:
Maybe it would be helpful to call this out as a note in the sourcing guide.  I had a similar problem with my V0 panels I ordered from TAP and it never occurred to me that it might be an issue.

insurgus, 2021-06-01:
Putting a note in the 2.4 manual regarding fitment.

Closed 2021-06-10.

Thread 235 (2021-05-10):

Bowden retainer does not fit over a T-nut

NameOfTheDragon, 2021-05-10:
I note that the door hinges were updated a few days ago so that they now fit over a "roll-in" T-nut. The Bowden retaining clip suffers from the same issue.

NameOfTheDragon, 2021-05-10:
Never mind - it was probably intended to use hammerhead T-nuts with the hinges and clips.

jurisv, 2021-05-10:
Please note that original Misumi nuts with clip on the side are the same length as the hammer-head T nuts. Unless cheap Chinese nuts with ball are used, there should be no issue. In fact those roll in ball spring nuts are so bad quality that they should no longer be on the list. I purchased ones that were in the sourcing guide last year, and again this spring. They all have manufacturing defect where the width of the nut is too wide for proper insertion. 8mm+-0.1mm vs 8.3..8.4mm actual size. I reordered from multiple vendors on Amazon and they all were the same wrong size.

aureumlocus, 2021-05-10:
I got a Formbot kit a month ago. I'm aware of the limitations of the kit but hadn't seen the T-nut issue before. I just checked and the T-nuts I have (M3 and M5) at 8.13 and 8.11 mm wide respectively are just outside the tolerances you mentioned. I'm hoping they'll be OK. I've just started assembling the frame and have just inserted the M5 nuts for the heated bed. They went in relatively easily. I haven't tried to get them out though! 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

Closed 2021-05-10.

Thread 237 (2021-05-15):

[V2.4] SKR 1.4 AB motor pinout different in config vs guide

cbc02009, 2021-05-15:
The motor connections in the guide for AB motors are opposite what they are in the config:

wiring guide (pg 2):
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

config:
```
[stepper_x]
##	Connected to X on mcu_xye (B Motor)
...
[stepper_y]
##	Connected to Y on mcu_xye (A Motor)
...
```

Someone pointed this out on discord so I figured I'd create an issue.

insurgus, 2021-06-01:
Some discussion has to be had internally to decide how we are going to standardize this. We used to use A/B and then added X/Y and it has caused some confusion in the community. That coupled with the fact that the configs call for X/Y/Z for the MCU is certainly something we should discuss.

stephenlawrence, 2021-07-14:
I prefer xyz vs. A/B myself.

NameOfTheDragon, 2021-07-14:
> I prefer xyz vs. A/B myself.

Z makes perfect sense but X/Y does not make sense in the context of a CoreXY mechanism, since both motors cause movement in both X and Y. Only by moving both motors is it possible to move in just X or just Y. So which one do you call the X motor and which one the Y motor? It has to be "neither". A/B doesn't really make much sense either because that still doesn't make it obvious which motor is being referred to unless you look it up on a diagram. In my view, it makes more sense to call them "Left" and "right", because one of them is on the left and the other is on the right. That's still a bit ambiguous because it depends which direction you are looking from, so I would say it is even more clear to call them "Back left" and "Back right" or "BL" and "BR". I think thats as good as it gets in terms of disambiguation and having a name that is "intuitively obvious".

stephenlawrence, 2021-07-14:
Ok, I changed my preference now to BL and BR. :)

cbc02009, 2021-07-15:
I agree back left and back right (BL and BR) makes the most sense.

mathiasm74, 2022-02-17:
I've also noticed this issue. I connected the A motor (BR) to MOTOR0 and B motor (BL) to the MOTOR1 on my Octopus, and the toolhead homed away from the x endstop. The [only solution](https://docs.vorondesign.com/build/startup/#v2-1) to this is to swap the wires. This seems wrong, going by what the documentation says.

But I'm confused about the source of this problem. I would assume the Voron documentation is correct, but this yields the wrong result. I've noticed that the motors in the illustration appears to point in the wrong direction compared to how they are on a 2.4. Is it possible that they were reoriented compared to an earlier version, and that the A and B has effectively swapped places?

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

Closed 2022-02-23.

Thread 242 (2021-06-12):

Probe malfunctioning crash prevention routine

no-mana, 2021-06-12:
I was motivated to implement a simple routine to prevent a crash due to a dead probe when, after G28, I saw my printer dig into the bed doing the QGL. I found out that the probe was not working after just 1 month of use (mainly doing meshing to solve my bed flatness issues).

I believe this is something that might be useful for others considering the doubtful QC and disparity of the probes used with the Voron 2.X.

The idea is to home (G28) then query the probe at a safe position/height where it is known to trigger. Check if it triggered, if not raise error. Takes less than 10 sec.

Is this something PR worthwhile?

a1co, 2021-06-13:
That sounds like a good idea. I cannot check now, but i belive my probe sould light ub when the z endstop is triggert. Then that would not cost any additional time.

julianschill, 2021-06-13:
This can be done with a macro. Check my CHECK_FLEXPLATE macro here: https://github.com/julianschill/CeBe_config/blob/cafaae847d028ac051ec81ee0b90436a6cc46ce3/macros.cfg#L66

a1co, 2021-06-13:
>
>
> That sounds like a good idea. I cannot check now, but i belive my probe sould light ub when the z endstop is triggert. Then that would not cost any additional time.

That was nonsense: The z endstop is behind the bed. But there could still be a screwhead for probe testing placed.

knackmanic, 2021-06-13:
>
>
> This can be done with a macro. Check my CHECK_FLEXPLATE macro here: https://github.com/julianschill/CeBe_config/blob/cafaae847d028ac051ec81ee0b90436a6cc46ce3/macros.cfg#L66

Yup, that's exactly what I meant by routine (including a macro that does the check in the config). IMO, it'd be a good thing to add in the doc (maybe like a "safety" configuration section?) I've seen a few user in the discord losing their probe and digging a nice hole in the plate. The homing sequence could also be done at lower Z current which would help prevent catastrophic issue  in case your forget to put the Z pin, the head got stuck somewhere during the homing and it's not underneath the Z pin / other bad luck, etc.

raymondh2, 2021-09-20:
Inactivity

Closed 2021-09-20.

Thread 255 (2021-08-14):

AB Idler Belt Wear

chrisingham05, 2021-08-14:
I have a suggestion for improving the AB front idlers as I've had some damage to my belts due to how they are designed. Currently, the idlers are tightened using a screw at the front which are aligned to the centre of the idler, however as the belt idler is either at the top or bottom depending on which side it sits this creates a rotational force which mis-aligns the idler bearing giving it a slight angle. This angle causes the belt to rub at one end causing wear to the belt. I suggest moving the screw so that it is in line with the centre of the idler bearing so that there is no rotational force. For my printer, I plan to make a few spacer wedges that I can stick in the idler to stop this rotation, but just moving the tensioner screw in the design would fix this quite easily. Only downside is it would not look symmetrical from the front.

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

chrisingham05, 2021-08-14:
Slight damage to the belt found so far

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

chrisingham05, 2021-08-17:
Temporary solution is to measure the gap between the red carriage and back of the idler with callipers to see the distance when the belts are tensioned, then printed small spacer blocks for each side to align the red carriage. Using one block at the end of where the belt meets allowed me to change the angle of the red carriage by tightening or loosening the screw. Appears to have improve the situation for now. Obviously on the right the block is at the top and on the left the block is at the bottom. Note, the picture is the correct way up, I assembled the red carriage upside down but that doesn't affect the printer or this issue.

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

ServAlex, 2021-08-17:
I also experience this issue on B belt, haven't verified culprit yet

yonkiman, 2021-09-04:
I have the exact same wear issues around front idlers on A and B belts.  Your explanation sounds right - may try to address by twisting idler frame forward or backward before clamping down with vertical pin.  Would like to address before I re-belt…

chrisingham05, 2021-09-06:
Since fitting the spacer blocks I've not noticed any more wear on the belts

1ucket, 2021-09-06:
Have the same issue, for me it even cut a notch into the belt through which it is now leaving the idler.
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

DanJunior78, 2021-09-06:
Would be a good idea to redesign it, as you mentioned, test it and do a push request.
I'll soon build my second V2 and i could also try it.
In my first I've same issues.

ServAlex, 2021-09-06:
> Have the same issue, for me it even cut a notch into the belt through which it is now leaving the idler.
> 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

this one is really strange, I don't know what part could do that, the only guess is the flange of the idler, but to do that your belt have to be on top of it which would be quite noticeable.

1ucket, 2021-09-06:
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

It would become nearly completely stuck in the rear left corner (aka the part where the belt would leave the idler). So yeah, it was quite noticeable.

GadgetAngel, 2021-09-26:
> Temporary solution is to measure the gap between the red carriage and back of the idler with callipers to see the distance when the belts are tensioned, then printed small spacer blocks for each side to align the red carriage. Using one block at the end of where the belt meets allowed me to change the angle of the red carriage by tightening or loosening the screw. Appears to have improve the situation for now. Obviously on the right the block is at the top and on the left the block is at the bottom. Note, the picture is the correct way up, I assembled the red carriage upside down but that doesn't affect the printer or this issue.
>
> 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

Where is the parametric .stl file for the red carriage spacer blocks that I can print out for when I do my Voron 2.4 build?  I really do not want to damage by High Temperature Gates Belts!

1ucket, 2021-10-21:
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

There's a [guide ](https://docs.vorondesign.com/community/support/pull_request_guide.html) on how to add your mods. As @DanJunior78 said just add it to VoronUsers/tree/master/printer_mods.

netweaver1970, 2021-10-21:
Another (more adjustable and skinnier solution) https://github.com/Ramalama2/Voron-2-Mods/tree/main/Front_Idlers

GadgetAngel, 2021-11-27:
> Another (more adjustable and skinnier solution) https://github.com/Ramalama2/Voron-2-Mods/tree/main/Front_Idlers

yeah, I just found this suggestion.  Why doesn't Ramalama2 submit it to the VoronUsers mods branch?

I also see that Ramalama2 has the Front_Idlers offset for the GE5C mod and his design also uses a PIN in stead of a M5 bolt to align the idlers.  Thanks for the suggestion.

DaddyBender, 2021-12-04:
Please excuse me if I don't have the terminology quite right.

I was going over the latest f3d, and I think I found belt-to-belt contact?
Example:
If I remove the exterior parts to look at the idler bearings, it looks like the z belts are rubbing against the A/B (?) belts?

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

GadgetAngel, 2021-12-04:
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

I was looking at the belts of the Voron 2.4 assembly model also.  If you look the belt path does not fit the idlers, I think the model has an error in it.  To redraw the belt path to make if fit as it should would take time.

But I agree the model does show the belt path is off in places.

Galifrey1965, 2021-12-22:
I reprinted my tensioners today so they fit tighter around the carrier and after nipping up the M5 bolt they sit square no problem. However, seeing as this is down to print tolerances and poor design, I can see how Chrisingham05's design is much better and avoids running the bolt through the split in the joined carrier. Overall I cannot help but wonder how the design team missed this as a potential weakness.

Closed 2022-02-23.

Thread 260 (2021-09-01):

[V2.4] Manual Enhancement: Adding Comment on VHB, and some revamps.

khay8485, 2021-09-01:
Hello friendly Admin who reads this,

as i was in the last steps of building my V2 i found a page in the actual manual which i think could be added with an information that can be copy-pasted from a few pages before. Therefore i scrolled through the entire manual again to mark some spots that may be confusing.
- Page 23 shows the old motor mount, but i think you are aware of that.
- Page 34 shows the old printed part for the z endstop pin, maybe a comment about fitting should be added.
- On Page 78 lower left picture doesn´t belong there and can cause confusion. In addition the upper left pic on page 79 could be fitted to page 78 after deleting the wrong one. Then you would have a closed workstep.
- Maybe a hint on Page 99 that there are two different parts "belt_guard_**a**_x2.stl" and "belt_guard_**b**_x2.stl". They are only slightly different but if you know that they are, you can realize which to mount on each corner.
- Finally page 106, which shows mounting of the bottom panel. I assume there has to be VHB to fix the clips and latches to the panel? If so, just copy the comment on VHB from page 102. If not, a description on how to fix the hinges would be nice.

Nevertheless, thank you for all your time and effort to create and maintain such a detailed manual.

greetings
khay

simonaaker, 2021-09-04:
62 and 63 should switch order

Closed 2022-02-23.

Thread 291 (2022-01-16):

Problems with the provided .stl filesV2.4 350mm

Schmiddy84, 2022-01-16:
Hello everyone, I have problems with some .stl files. Everything is displayed correctly in the slicer, but in some layers I have errors when printing, such as printing straight through a hole or a radius is missing in the outer contours of a layer.

I can avoid these errors by creating the .stl files myself from the supplied .step file. However, I now have problems with generating the "skirt" parts myself because the .step file does not seem to show a size of 350. How do I get the CAD files from the 350mm version. Many Thanks.

Greetings Schmiddy84

GadgetAngel, 2022-01-16:
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

@Schmiddy84 The Skirt files for the 350mm build are in the Fusion 360 (or .f3d file) for 250mm and in the STEP file for the Voron 2.4.  If you are using the .f3d files for the Voron 2.4 , then you will have to go to the "lower valance" and select the skirt of interest.  The 250mm will be displayed, but if you goto the the "Body" folder of the skirt you will see three bodies included in the item. In the Skirt Body, only one body is visible (the 250mm is visible). Just turn off the 250mm skirt and turn on the 350mm skirt.

If you are using the .step file for the Voron 2.4, then all the skirt bodies should be turned on, because the .step file will not save them if they are not visible.  So If you can not follow what I said to do above, just down load the Voron 2.4 model in .STEP format and you will see all three skirts turned on all the way around the printer.

I hope this helped.

Schmiddy84, 2022-01-16:
Thank you for your help. I had the step file open the whole time and couldn't find the 350mm option. Now that I opened the .f3d file I could find the hidden skirts.

Schmiddy84, 2022-01-16:
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

I was able to find all skirts except for the front/rear skirt b. Strangely enough, this can only be found in the 250mm version.

Schmiddy84, 2022-01-16:
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

Closed 2022-01-16.

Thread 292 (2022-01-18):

V2.4 BTT Octopus printer.cfg - [stepper_z] motor direction should be reversed

310weber, 2022-01-18:
@cbc02009
Z stepper motors should alternate directions.  In the current [V2 Octopus config example](https://github.com/VoronDesign/Voron-2/blob/Voron2.4/firmware/klipper_configurations/Octopus/Voron2_Octopus_Config.cfg) both Z and Z1 rotate in the same direction.  This causes Z to move down when Z1-Z3 move up (and loud belt slipping noises).

[stepper_z] should be reversed.

Current:
```
[stepper_z]
step_pin: PF11
dir_pin: PG3
enable_pin: !PG5

```

Should be:
```
[stepper_z]
step_pin: PF11
dir_pin: !PG3
enable_pin: !PG5
```

cbc02009, 2022-01-18:
The inversion/non-inversion of any of the steppers in the default config is purely for example purposes. It can change from stepper to stepper as the are wired differently between vendors and even sometimes with motors from the same vendor. This is makes it impossible to have one stepper config that works for everyone.

The startup documentation details the process for adjusting the z steppers so they all move in the same direction.

310weber, 2022-01-19:
I get that, but the most common scenario is that a builder will use one brand/model of stepper and wire them all the same way. In this scenario the Z motor directions should alternate (e.g. Z & Z2 reversed and Z1 & Z3 not reversed). That way at least they will all move up or all move down together. I think it makes sense to have the example config align with the most common scenario rather than the unlikely scenario that someone happens to wire the Z motor backwards compared to all the others.

In my case I just happened to miss that one motor moving down rather than up first during the stepper_buzz step. So, when I went to do X homing one corner of the gantry moved down while the other three moved up. It made horrible belt skipping noises. Scared the crap out of me. Totally my fault for missing it, but I'd bet this simple change would save others from the same fate.

cbc02009, 2022-01-19:
that's a fair point. I'll work on PR.

310weber, 2022-01-19:
Thank you!

Closed 2022-01-19.

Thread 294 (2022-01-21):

Uneven / Incosistant layers on X-axis

kubusAB33, 2022-01-21:
## Problem:

Uneven / Incosistant layers on X-axis, while the proplem does not occur on Y-axis.

Printer: Voron V 2.4
Hardware all stock
Board: BTT Octopus
Stepper Drivers: TMC 2209

## Trials to solve:

-	Checked all idlers/pulleys if they can rotate freely and without play. Check
-	Checked all screw if sitting tight (gantry, hotend, frame). Check
-	Did Z-joint procedure (losen M5 bolts, do QGL, fasten screws afterwards) sveral times. Check
-	Tried differend belt tensions. Check
-	Check if belts are eventy tensiond. Check.
-	Printed test part on several bed locations. Check
-	Tried printing with differend speeds and accelerations. Check.
-	Tried printing with and without Input Shaper. Check
-	Tried printing with and without Preassure Advance.
-	Doublechecked toolhead if there is any wobble/play. Check
-	Cleaned nozzle. Check
-	Checked print bed for play/wobble. Check
-	Checked if toolhead is moving in X when gantry is moved in Y only (maually). Check.
-	Checked x-rails for propper alignment. Check.
-	Checked different filaments and print temperatures. Check.

Now I ran out of ideas.
Since I checked all the mechanical parts, I doubt, that the problem is caused by them, even if it clearly looks like a mechanical issue.

### Left over ideas:

-	Something is wrong with the synchronization of A and B motor
-	Something is wrong in the firmware I use
-	Something is wrong with the connections of the motors
-	Something is wrong with the current settings oft he steppers
-	There may be minimal play in Y, when toolhead moves in X direction

That’s just my thoughts. I hope for some input, support and help for solving my problem.

Thanks a lot in advance!

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

kubusAB33, 2022-01-21:
Here's an example of a cylinder.
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

aaron-hentschel, 2023-06-11:
I have this exact same issue on my Voron 0.2 (although not as bad as kubusAB33).  What was the fix for this?

Closed 2022-01-22.

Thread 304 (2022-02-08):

generic cable chains documentation and bend radius

bubnikv, 2022-02-08:
1) Document how the generic chain should bend around the tool head. The chain shall not be allowed to bend sharply upwards at the tool head as in https://www.reddit.com/r/voroncorexy/comments/sn6f6f/voron_v24_serial_request_z_rex_8520/
Correct:
https://www.reddit.com/r/voroncorexy/comments/smz6ma/voron_24_serial_request_discord_homewerken0078/

The trick is that one end of the generic chains rotates freely while the other end's rotation is limited. The limited rotation end shall be mounted high while the freely rotating end shall be mounted to the aluminum extrusion.

2) The number of links for the generic cables is not documented. This likely costs many of us many hours trying to find out ourselves, or building incorrectly. Also please document how to open the chains, I pried couple of links violently breaking some of the latches before finding out that one shall use a small screwdriver to open the links.

3) The generic chains don't like to bend at such a sharp angle, at least those delivered with the Formbot kit. Also the Formbot provided PTFE cables are quite rigid. I don't like to break those expensive high quality cables by bending them sharply. I would rather sacrifice a centimeter or two of Z height for durability of X/Y cables. Thus I would like to get at least the X cable mounted higher. I am re-modeling the X cable mount to align the bottom of the mount with the top of the E motor and to add a zip tie mount for the E cables. The Y chain end is a bit higher than the X chain end, however the chain bends it upwards most of the time, thus the Y chain bends under a higher radius than the X chain. I would still like the Y chain to be mounted higher.

It may also be a good idea to use more links than usual. The X chain then would collide with the left rear Z idler at the very top position with Y above 300mm for my 300mm build, however one may configure Klipper to only move Y above 300mm when homing, thus avoiding this collision.

3) Offer a Z mount for the generic chains.

4) As mentioned in https://github.com/VoronDesign/Voron-2/issues/245 the sourcing guide does not specify enough of screws.

5) Update the manual to explain that a single screw is sufficient to mount the generic chains to the aluminum extrusions. This is already made clear in the Trident manual, which I suppose recommends the generic chains primarily.

raymondh2, 2022-02-09:
Issues 1, 3#2, and 5 are being worked on for 2.4r2
Issue 2 is documented for Igus Chains but will not be for generic chains as it varies.
Issue 3#1 has not proved an issue with wires breaking when using PTFE
Issue 4 is already covered by another open issue.

I hope this answers your concerns

Closed 2022-02-09.

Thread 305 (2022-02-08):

Octopus board and hall effect XY end stop board

bubnikv, 2022-02-08:
Please document that:

1) The Octopus board end stop inputs are 5 volts tolerant, thus it is possible to connect a 5V end stop input in there. I suppose other STM based boards are similar.

2) The hall effect XY sensor requires 5V, however it outputs 3.3V. Formbot provided cable powers the board from 3.3V. Please document that the builder may need to split the cable provided by some kit providers to power from 5V, not 3.3V

bdbell, 2022-02-08:
This would fit better in the documentation site.

bubnikv, 2022-02-09:
Regarding wiring: There is a risk that any of the mains wring including the bed heater wire breaks off and touches the metal frame.  The metal frame shall be grounded.

raymondh2, 2022-02-09:
As documented you should follow your local code when it comes to mains wiring. As we can't document it all we don't. We put in general best practices. The first two issues are more docs repo issues.

Hope that explains it for you :)

bubnikv, 2022-02-09:
> As documented you should follow your local code when it comes to mains wiring. As we can't document it all we don't.

This is one that I strongly disagree with. Grounding a metal frame is something one shall do. I wonder how many Voron builders did not do that.

According to a local code, most likely the vast majority of the Voron builders are prohibited to do the mains wiring themselves. We cannot expect the builders to study the code. General safety guidelines should be given.

bubnikv, 2022-02-10:
The SSR shall be grounded through its DIN rail. How many of Voron builders did it? Did you do that? Did you read your local code?

The Trident and Voron 0.1 moving bed is a shock hazard, I don't think it would pass your local code even if grounded, because if the grounding wire breaks first and the mains second, it will still kill you. With a moving bed you would likely either need a
https://en.wikipedia.org/wiki/Residual-current_device, some kind of automatic testing of the ground wire or a complete insulation of all metal parts.  Voron 2.4 may pass because the wire does not move.

The plastic sheet of the electronics compartment shall likely be a fire retardant kind.

bubnikv, 2022-02-20:
> The hall effect XY sensor requires 5V, however it outputs 3.3V. Formbot provided cable powers the board from 3.3V. Please document that the builder may need to split the cable provided by some kit providers to power from 5V, not 3.3V

BTW I just found out that the issue is not the Formbot kit, but the Octopus board documentation, it seems the documentation is outdated. I have created them an issue.
https://github.com/bigtreetech/BIGTREETECH-OCTOPUS-V1.0/issues/105

That was a costly experiment, as the Formbot cable uses unusual color coding for the cables, thus I connected 5V to the hall effect outputs and fried the chip on the hall effect board. I was lucky to have the fried part on some other board, so I was able to fix the hall effect board quickly.

Closed 2022-02-09.

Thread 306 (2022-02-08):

metal corners on frame?

bubnikv, 2022-02-08:
After adjusting the frame with blind joints carefully, I wonder whether the frame will not move at the blind joints when the quite heavy machine is transported multiple times.

I have seen a mod where aluminum corner joints were used in addition to blind joints.
https://jan-griffioen.synology.me/voron-2-4-corexy-printer-300x300mm/

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

IMHO such reinforcement of the frame is quite valuable and not too expensive. Does it make sense?

https://www.aliexpress.com/item/4000929742684.html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

https://www.aliexpress.com/item/33041512892.html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

https://www.aliexpress.com/wholesale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

raymondh2, 2022-02-09:
As stock the current frame is quite rigid when tightened properly. And the printed parts offer indexing to keep the extrusions from twisting drastically.

raymondh2, 2022-02-09:
This is something we don't think is needed by most builders. If it becomes an issue later on we can reopen this issue :)

Closed 2022-02-09.

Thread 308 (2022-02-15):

Convert the used CAD projects in Free Software alternative as required by GPLv3

Kreyren, 2022-02-15:
Currently the design depends on nonfree libraries required to work with the proprietary format `f3d` used in proprietary Fusion360 which conflicts with GPLv3 as it requires that the design be workable using Free Software solution[https://www.gnu.org/licenses/gpl-faq.en.html#FSWithNFLibs].

Proposing to convert the used project files in FreeCAD+OpenSCAD/LibFive to make the workable in a Free Environment while making them more functional.

Note that using such software management makes the designs more:
1. Functional - Enabling modular design instead of the current fixed
2. Robust - Through the possibility of test implementation in OpenSCAD/LibFive e.g. failing Quality Assurance ("QA") on a merge request if a hole with expected diameter of 10mm>=5mm is outside of the standardized scope.

### Motivation

During my research for my CoreXY printer design i found this project and i would like to work on it and adjust it for my computing* as it saves me a time and resources on the design.

* Namely LinuxCNC compatibility and ability to use tool-changer (https://forum.linuxcnc.org/additive-manufacturing/44926-considerations-for-linuxcnc-for-a-custom-ender-3-based-3d-printer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)

---

If such change is in the scope of this project then i would like to contribute to the effort namely:
1. Converting the provided STL files in OpenSCAD/LibFive
2. Working on standardization of the parts in FreeCAD and generated assembly
3. Cost optimization of the project e.g. using printed parts for the structure instead of aluminium extrusion

khumarahn, 2022-02-15:
Converting voron files to freecad or openscad is way too much to ask from the developers. Imagine how much time that takes!!!

You can probably use the step files which are provided and can be used in freecad. Step is the universal format for exchange between cads, so I'd argue that there is no violation of GPLv3 here.

Kreyren, 2022-02-15:
> Converting voron files to freecad or openscad is way too much to ask from the developers. Imagine how much time that takes!!!

I calculated it on 814.2 EUR for an engineer working non-stop at the average minimal wage in the EU, feel free to correct me.

So I agree that it's a lot of work, but i am willing to work on it as it's still less resources in comparison to making my own design from the scratch.

> Step is the universal format for exchange between cads, so I'd argue that there is no violation of GPLv3 here. -- @khumarahn

I find that being a valid argument, but i see it as "distribution of a built-binary using a proprietary solution" scenario as the imported files can't be changed easily in a FreeCAD that expects parametrized objects or in OpenSCAD/LibFive that expect functional objects.

raymondh2, 2022-02-15:
Please do not ping people into this conversation. We will look at this issue when we have time

nemgrea, 2022-02-15:
converting the cad to ANYTHING other than the Standard for the Exchange of Product Data (.STEP) is counterproductive.

Kreyren, 2022-02-15:
> This is not a commercial project, the monetary estimates don't mean much...  -- @khumarahn (https://github.com/VoronDesign/Voron-2/issues/308#issuecomment-1040339679)

I am aware, my intention was to calculate the amount of work that would be needed to realize this proposal where i usually use EUR/USD since calculating in terms of working hours is often not accurate enough.

>  Step files can be worked with in freecad, and parametrized models often don't exist in f3d either. -- @khumarahn (https://github.com/VoronDesign/Voron-2/issues/308#issuecomment-1040339679)

Thus why i said "easily" as using the STEP files for simulations and changing them gets really annoying over the time which then requires the object to be redefined for larger changes.

> converting the cad to ANYTHING other than the Standard for the Exchange of Product Data (.STEP) is counterproductive. -- @nemgrea (https://github.com/VoronDesign/Voron-2/issues/308#issuecomment-1040341372)

I do not propose changing the output formats just the solution used to generate them.

> Please do not ping people into this conversation. We will look at this issue when we have time -- @raymondh2 (https://github.com/VoronDesign/Voron-2/issues/308#issuecomment-1040341032)

Noted, sorry! i am used to pinging people.

raymondh2, 2022-02-15:
So first off let us start with the use of STEP files. STEP files are an ISO standard, ISO 10303-21, used by all major CAD packages to allow interchange of data between them.

Second some of our developers are significantly more comfortable in the CAD packages they use and won't likely ever be changing, hence the use of STEP files allowing easy exchange of the files.

Kreyren, 2022-02-15:
> So first off let us start with the use of STEP files. STEP files are an ISO standard, ISO 10303-21, used by all major CAD packages to allow interchange of data between them. -- @raymondh2 (https://github.com/VoronDesign/Voron-2/issues/308#issuecomment-1040349351)

Again i am not proposing to change the output, i only propose changing the CAD solution used to generate these files.

> Second some of our developers are significantly more comfortable in the CAD packages they use and won't likely ever be changing, hence the use of STEP files allowing easy exchange of the files. -- @raymondh2 (https://github.com/VoronDesign/Voron-2/issues/308#issuecomment-1040349351)

I find it hard to believe that the proposed solution will be a problem in terms of a comfort as it's significantly more user-friendly and functional (excluding topological optimization as that is to my knowledge a thing made by proprietary industry and we have to make it from scratch in our solution due to them not sharing, but it works sometimes better then the alternative).

FWIW So far everyone who i convinced to try FreeCAD and OpenSCAD/LibFive (12 out of 12 ppl) found the solution significantly less flustrating and functional, but there seems to be a learning curve for those who migrate from Fusion360 so be aware of that if you want to migrate.

> this is a misunderstanding of the license and is not a requirement. -- @nemgrea (https://github.com/VoronDesign/Voron-2/issues/308#issuecomment-1040355881)

I find this being a common argument, but from my conversation about hardware freedom with the license authors (https://lists.gnu.org/archive/html/libreplanet-discuss/2022-01/msg00059.html) i understood that using proprietary solution to produce the Free Hardware Designs in questions is fine as long as the use of a proprietary solution does not infringes on one's rights to use, study, improve and redistribute.

In this case the design depends on non-free libraries that obstruct the right to:
* improve - as i can't contribute to this project without using Fusion360 as the use of the proprietary libraries and formats is not compatible with functions and formats used in Free Software CAD solutions and it's implementation in the Free Software solution would be a violation of AutoCAD's license.
* use - I can't adjust this design for my computing as it's not usable in a free environment.

So in good faith i believe that this argument would be valid if Fusion360 exported it's project file in an non-proprietary format so it's still violation of the GPLv3 in terms of depending on non-free libraries that do not fall under the `System Libraries` term.

nemgrea, 2022-02-15:
> improve - as i can't contribute to this project without using Fusion360 as the use of the proprietary libraries and formats is not compatible with functions and formats used in Free Software CAD solutions and it's implementation in the Free Software solution would be a violation of AutoCAD's license.

yes you can, nothing preventing a step file from being opened or edited in any of the programs listed. so this is not true.

> use - I can't adjust this design for my computing as it's not compatible with a free environment

yes you can, nothing preventing a step file from being opened or edited in any of the programs listed. so this is ALSO not true.

raymondh2, 2022-02-15:
As we have no interest in forcing a CAD package on our devs I am closing this. You can always whatever CAD package you want to open the STEP file we provide and make changes to it.

Kreyren, 2022-02-15:
> i contribute to this project heavily and i dont use fusion360 at all.. -- @nemgrea (https://github.com/VoronDesign/Voron-2/issues/308#issuecomment-1040393055)

Can you elaborate how? Do you just submit the STEP files for the project developers to adapt them in Fusion360 project? Or is the development oriented around the STEP files with the fusion360 being used as a form of tool configuration without hard dependency on the design?

> As we have no interest in forcing a CAD package on our devs I am closing this. You can always use whatever CAD package you want to open the STEP file we provide and make changes to it. -- @raymondh2 (https://github.com/VoronDesign/Voron-2/issues/308#issuecomment-1040404101)

Alternatively to "Forcing FreeCAD" the objects can be redefined in OpenSCAD which can then be imported in both Fusion360 and FreeCAD to work on them so it would no longer have a hard dependency on Fusion360 while enabling other solutions that would then be only used for
1. prototyping - As OpenSCAD is not the tool for that
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

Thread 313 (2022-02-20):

Q: Why did you decide for the gantry to move on Z axis?

Kreyren, 2022-02-20:
I wasn't able to find the answer in the repo so i am asking here:

Why did you decide for the gantry to move on a Z-Axis over mounting it to the top of the chassis and move the bed on Z axis?

Doing quick simulations it seems that this should cause an inconsistent printing at 800 (+-100) mm/s due to the momentum of the gantry?

or like is handling of this situation through firmware better in comparison to the mounting it to the top and move bed on Z axis?

Kreyren, 2022-02-20:
Or like is this projected to have a CNC rotor or printing at the angle in the future to make this design decision now?

BeardedTinker, 2022-02-20:
@Kreyren  - Voron 2 didn't change anything in terms of static bed - you are probably mistaken about versioning - V2 is not version but model 2 - you still have option to got for Voron Trident (previously 1.8).
Remember that number doesn't indicate version (as in newer model) but model number.
Also, by having static bed, lower centre of gravity, helps with stability and as a matter of fact allows higher speeds with this.

Kreyren, 2022-02-20:
@BeardedTinker does it still enable higher speeds assuming that the gantry mounted at the top with moving bed has a lower center of gravity (e.g. by adding a huge weight to the bottom of the printer)?

BeardedTinker, 2022-02-20:
Sorry, don't follow you - Moving bed (Z) is higher and as such has higher centre of gravity, while, fixed bed at the bottom has lower.. So not sure what you were asking? In terms of acceleration - I suggest that you join the Discord server as you will get more detailed and proper answer as not everyone is here or checks the GitHub.
But I have no problem with 10k accelerations on my V2, for printing, I go for quality so speed is not that important for me.

Kreyren, 2022-02-20:
> Sorry, don't follow you - Moving bed (Z) is higher and as such has higher centre of gravity, while, fixed bed at the bottom has lower..  -- @BeardedTinker (https://github.com/VoronDesign/Voron-2/issues/313#issuecomment-1046298972)

You said that it's about a center of the mass that enables it to be faster.

So assuming that both solutions have a weight added to the bottom of the printer to keep the center of the mass low -> Is the moving gantry still better?

> I suggest that you join the Discord server as you will get more detailed and proper answer as not everyone is here or checks the GitHub. -- @BeardedTinker (https://github.com/VoronDesign/Voron-2/issues/313#issuecomment-1046298972)

I don't use discord, but noted.

> But I have no problem with 10k accelerations on my V2, for printing, I go for quality so speed is not that important for me. -- @BeardedTinker (https://github.com/VoronDesign/Voron-2/issues/313#issuecomment-1046298972)

10K of what? m/s2 ?

BeardedTinker, 2022-02-20:
You can find manual and CAD files here and also you can go to https://docs.vorondesign.com/ for additional information.
Most of the answers to your questions are there.
Also, for general questions and assistance Discord server is preferred way to go.

Closed 2022-03-16.

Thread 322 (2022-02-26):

Rear centre is about 4mm too big.

Macmagoo, 2022-02-26:
The Rear Centre Skirt is about 4mm too big it does not fit Voron 300.

stvptrsn, 2022-02-27:
> The Rear Centre Skirt is about 4mm too big it does not fit Voron 300.

Hi Macmagoo, can you provide any pictures?  I've printed an installed the parts on a 300 build so I'd like to see if something else might be going on.

Steve

Macmagoo, 2022-02-27:
Hi Steve, I hope the attached pictures help. It is my first Voron so perhaps it is something I have done. I am going to reprint it at some point today with a 4 mm reduction in length.

Thanks to the Voron Team for the work you all put into the design.

Regards

Andy
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

stvptrsn, 2022-02-27:
> Hi Steve, I hope the attached pictures help. It is my first Voron so perhaps it is something I have done. I am going to reprint it at some point today with a 4 mm reduction in length. Thanks to the Voron Team for the work you all put into the design. Regards Andy
> […](#)
> On 27 Feb 2022, 04:56 +0000, Steve Peterson ***@***.***>, wrote: > The Rear Centre Skirt is about 4mm too big it does not fit Voron 300. Hi Macmagoo, can you provide any pictures? I've printed an installed the parts on a 300 build so I'd like to see if something else might be going on. Steve — Reply to this email directly, view it on GitHub, or unsubscribe. Triage notifications on the go with GitHub Mobile for iOS or Android. You are receiving this because you authored the thread.Message ID: ***@***.***>

The pictures do not appear to have come across. Are you on the Voron discord?  You can DM me there.  I doubt you need to re-print.  How do the side pieces line up?  Do you have the belt guards installed and are they pressed up against the Z drive modules?

Steve

Macmagoo, 2022-02-27:
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

Macmagoo, 2022-02-27:
I have attached them here.

stvptrsn, 2022-02-27:
You have mismatched parts there.  The side opposite the power inlet is the old version or a front piece.  You need the keystone piece.

Steve

stvptrsn, 2022-02-27:
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

Closed 2022-02-27.

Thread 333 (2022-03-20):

M3 Theaded inserts are missing dimensions

SMTDesigns, 2022-03-20:
The BOM states just a M3 threaded insert with no details and the r2 assembly manual on page 31 mentions dimensions in the BOM (which aren't there). There are so many sizes of m3 inserts that it can be confusing to people that have not used them before.

Suggest adding dimensions to BOM as indicated "M3 4.6mm diameter and 4mm to 5mm long"

chri-kai-in, 2022-03-27:
Good initiative ! Aside that, i see it difficult to get other heat inserts than those requiring 4mm bore holes on the market. This might by a local issue, but all suppliers capable of delivery in the "big A" marketspace provide heat inserts with 3.9 or 4 mm bore hole reccommendations. It is hardly possible to get sufficient grip with those in todays 4.7mm bore holes in all Voron parts. On top to manual improvements, it would be maybe even more helpful to adjust the holes diameter in voron parts to the majority of available heat inserts on the market. On top, i still see it feasible to melt inserts for 4.7mm holes into 4mm bore holes. Worst case it would require prior drilling with a 4.5mm drill bit. Other way round i found it difficult...

SMTDesigns, 2022-03-27:
I produce 3d printed rocketry bay parts. I have used thermal inserts for years and it is important that the physical hole is sized for the insert for strength. What may be the best route is to look at what is available now and move all inserts to the same physical size. I would not recommend setting a larger insert into a small hole. Too much plastic gets melted and literally pushed out of the way.  Not all parts could use a larger diameter insert without making the surrounding plastic larger for support of the insert.

nemgrea, 2022-12-13:
fixed

Closed 2022-12-13.

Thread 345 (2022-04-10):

Using unsafe and untested parts on BOM

Quickuser75, 2022-04-10:
I MAKE A SERIOUS WARNING TO PEOPLE THAT BUILD
THIS PRINTER
This is made by amateur that have no real safety in mind
I have been over your list of BOM and a lot of your parts listed and unsafe and don't hold any genuine safety certificate
Anyone that follow your list and be seriously accident and even death, one of your mains parts have not safety certificates

I have ordered all the parts use have listed and done real safety checks and have failed even an earth leakage test and main
I HAVE ALSO SEE A POWERSUPPLY THAT IS LISTED BURST INTO FLAMES AND SENDING 250V down the low voltage lines
You have picked most aliexpress parts and serious unsafe
This poses a serious health and safety concern

I warn anyone that builds and uses the BOM that the amateur  voron designer have listed

I work for a consumer election and industry company and do emi and safety tests on electronic even hobbies based
And this printer would as built would fall the test

Maybe the STL files would be safe upto a point
That is they would made correctly, I have designed parts that have been correct first time for the aerospace industries
I am looking it to this also

They offer a serial where you can show your printer working and the wiring, but that is not a emi or safety test

The only part of you use would be an e3d or any genuine hotend that go's through serious electronic and safety  tests

If you remove this safety concern from the issue,  I have made a screenshot and with again post on a number of social media platforms and will force me to create a video on YouTube and show you disconcerting interest in hobbies health and safety

SMTDesigns, 2022-04-10:
Please pass on the test results to the community here, so we can look at what you have done. Also, point out what parts specifically do not have certificates rather than just sending a general list of negative comments. The screen shot you made would be helpful also. Thank you.

Quickuser75, 2022-04-11:
Oh looks a rocket designer to vorons rescue, do you use a voron by any chance... maybe you should do the tests close my case

bdbell, 2022-04-11:
Actually, it's a really common part of the accepted scientific method to ask for someone else's test results as a starting point for proving or disproving something.  He is one of the designers and is openly looking for the evidence you have in order to start his investigation. If you have legitimate test results then please provide them as it would be helpful.

DrDMo, 2022-04-11:
Dude, just leave.

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

Quickuser75, 2022-04-11:
I don't have any of them I have sent them to the UK British standards to be investagated

bdbell, 2022-04-11:
> I don't have any of them I have sent them to the British standards in the UK to be investagated unlike the US we have powered to have item imported investagated for safety and the cases banned from entering the country

I look forward to seeing the results.

Quickuser75, 2022-04-11:
Github is unsafe to post personal information
As of this I will not be sending anything

I am posting to mind other that using aliexpress is unsafe very small procent of electronic are tested and just has a shiny sticker them can be get from ebay

Quickuser75, 2022-04-11:
I will not be responding again

Quickuser75, 2022-04-11:
Sorry SMTDesigns, when are you going to Make a better 3D Printer

DrDMo, 2022-04-11:
What an idiot.

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

shiftingtech, 2022-04-11:
I'm locking this, just to avoid any more aggression on any side

Closed 2022-04-11.

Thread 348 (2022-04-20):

Minor manual issues

gjsmo, 2022-04-20:
I am about halfway through my first build and I'd like to make some comments on the manual:

* Overall, printed parts are not labeled as to what their filename is. This can make determining which part is which difficult - it would be nice if these had labeling. A mark or other indication as to color (main or accent) would be very helpful as well.
* Page 20 "Belt Drive Shaft Assembly" - at least for the bearings and shafts I chose, bearings were press-fit. They also do not have dimensions listed. The best way I found to do this was to use a vice and a deep socket to push on the inner races, then when the bearing gets close to the final location move it by a millimeter or two and test fit. Dimensions and better instructions, possibly a printed press tool, would be helpful here.
* Page 23 "Z Drive Motor Mounts" - the motor mount no longer looks like this.
* Page 47 "Dual Rail Install" - the rail installation guide isn't usable for the the second rail to be installed, as it interferes with the first rail. Possibly this part could be updated with a shorter "leg" on one side? However, it appears it's beneficial to leave these loose as during carriage alignment they will probably bind.
* Pages 52 "Y Rail Install" and 53 "Front Idlers" - these would make much more sense if they were reversed, as page 52 references the idlers yet to be installed on page 53.

DunarDolorgiet, 2022-04-20:
Can you please check if you are using the current version of the manual?
First page bottom right should read: "VERSION 2022-04-09".

julianschill, 2022-04-20:
I think you are referring to the old manual, becaude most of this has been adressed with the 2.4r2 manual.
Regarding your second point: This shouldn't be press fit. You probably sourced the wrong shafts.

gjsmo, 2022-04-20:
You're both correct, this is the 2.4r1 manual ("2021.01.20") as well as 2.4r1 parts. I sourced 90% of everything last year, before 2.4r2 came out - figured I might as well finish it! I'm glad to see the manual has had a significant update, it does seem much clearer and well laid out now. Labeling of part filenames would still be helpful (it's nice to load up the STL sometimes to assist in locating the part), although I do appreciate the labeling of accent colored parts.

As far as the shafts go, there isn't an indication of which shafts to use apart from "5mm". If they shouldn't be press fit this should be clearer. As I'm in the US, a significant portion of the hardware is from McMaster - far faster than AliExpress. The linked shafts in the BOM do not have accurate tolerances or dimensions (at least not in English), so it's hard to tell what fit class is appropriate. I ended up with McMaster 1265K44 which are precision ground to 5mm +0.000/-0.005mm. Along with common 625-2RS bearings this is a press fit. To be clear, this isn't a problem functionality-wise, just assembly-wise.

There's a separate sourcing issue regarding US vs. European "2020" extrusion - again, it isn't entirely clear that there's a difference between the two, and the fastest to source in the US is from 80/20 (when I purchased the frame, Misumi was quoting something like 26 weeks lead time!). Unfortunately many components expect a 6mm gap rather than a 5mm gap so I've just been modifying those with a hobby knife. I figured I'd mention it on the topic of sourcing, I can make another issue if that would be more appropriate.

raymondh2, 2022-04-24:
Closing as the original issue is resolved

Closed 2022-04-24.

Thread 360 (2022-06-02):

mini12864_case_front fillet edge

whatthefilament, 2022-06-02:
When printing a new front case for my V2.4 I noticed that the heat-set inserts are designed to nestle in the front case body when inserting the accent piece. However, the cutouts for the heat-set inserts began halfway down the face making it very difficult to install the accent piece. Simply extending the cutouts up the face made the assembly and fitment much better.

Wasn't sure how to upload the modified files so here is a link to a repository for them. Please let me know if there is a better way.

https://github.com/whatthefilament/Voron-2.4-Mods/tree/main/Display%20Panel

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

stvptrsn, 2022-06-06:
The cutout for the heatset inserts have no lips to catch on anything when inserting the accent piece into the main housing so I do not see the need to extend those holes to the front surface.  I would check for print artifacts on your pieces that may be causing you difficulty.

Section analysis showing there are no surfaces that would prevent the accent piece from being inserted into the front piece.
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

whatthefilament, 2022-06-06:
I get what you're saying.

You can see the cutout fits the insert perfectly. However, when installing the front plate after the insert is installed it has a very hard time getting passed that edge. If that edge is gone. The heat-set insert slides in easily

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

stvptrsn, 2022-06-06:
Well there's the problem.  You insert the accent piece into the housing THEN insert the heatset while holding those two parts together.

whatthefilament, 2022-06-06:
Looks like my guide was corrupted. Which could have been part of the problem too.

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

Closed 2022-06-06.

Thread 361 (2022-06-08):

Afterburner and Probe Bracket heatset holes are 4.8mm instead of the 4.7mm used everywhere else

ChaosBlades, 2022-06-08:
This was fixed on the Afterburner CAD but not the Voron-2 CAD that contains Afterburner. STLs need to be updated as well.
https://github.com/VoronDesign/Voron-Afterburner/issues/15

In addition, the Probe Brackets are 4.8mm instead of 4.7mm as well.

Need to reprint these parts now because the heatset just falls into the hole instead of actually melting in.

nemgrea, 2023-03-03:
we will not be fixing this as long term the switch to StealthBurner will resolve this. thank you for the report though!

Closed 2023-03-03.

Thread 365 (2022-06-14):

Multiple discrepancies between STL and CAD models of electronics bay brackets

ReXT3D, 2022-06-14:
While assembling my 2.4v1 I was not thrilled with how loose the electronics bay components were on the DIN rails and I printed a number of upgraded brackets and mounts from 2.4v2 release STLs.  I then decided to make some additional changes to the parts and downloaded the F360 model to modify.  To my surprise, I immediately noticed differences in the models.  The items below are just two that I immediately identified and there could be more discrepancies.

1. **PSU_stabilizer_50mm.stl** does not have slotted hole for the PSU screw and will not fit without pushing up the decking material into the chamber.  The CAD model on the other hand has the correct slotted hole.  I also noticed on Discord that some people were posting photos of their PIF part kits that were printed with the STL model that has fitment issues.

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

2. **pcb_din_clip_x3.stl** is significantly different dimensionally from the CAD model.  In this case, my personal preference is actually for the STL model as it provides a much more secure mounting on the DIN rails while the CAD model clip is somewhat loose, especially when used alone such as on the 5V PSU.

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

DouglasJOlson, 2022-06-30:
I can attest the PSU Stabilizer 50mm STL as posted in the r2 STLs does not fit the recommended Meanwell PSU, the single Screw hole is off by 3-4mm, the adjustable screw hole in the CAD model works fine.  The STL should be updated with the CAD version to prevent further issues.

Jack-Lenders, 2022-10-10:
The STL for the Meanwell PSU does not align with the actual screw hole on the PSU. I think it is based on the height of the older DIN rail mounts.

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

DouglasJOlson, 2022-10-10:
> The STL for the Meanwell PSU does not align with the actual screw hole on the PSU. I think it is based on the height of the older DIN rail mounts.
>
The bracket in the CAD is correct, it uses a slot for the screw position, so can work with a wider variety of psu arrangements.
It needs to be updated in the downloadable STLs but as yet, this has not been done.

Jack-Lenders, 2022-10-10:
Posted this to bump your correct findings and maybe so the PIF team can update their plates and provide the correct bracket to new builds.

jsaintrocc, 2022-11-23:
Hi @DunarDolorgiet I've got a PR submitted with a fix for this. Could you help me get someone to review it? Happy to make any changes necessary and looking forward to contributing.

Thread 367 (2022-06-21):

btt mini 12864 connection issue- the leds on but nothing on the screen

mitofun, 2022-06-21:
Hi FOLKS how are you
could you please help me- cannot connect the btt mini 12864 to the skr 1.4t and raspberry pi 3 model A+
i follow the official instruction https://docs.vorondesign.com/build/electrical/mini12864_klipper_guide.html
have removed the R1 and C6 and uploaded the code to the printer.cfg -

**[display]
##  mini12864 LCD Display
lcd_type: uc1701
cs_pin: P1.18
a0_pin: P1.19
encoder_pins: ^P3.25,^P3.26
click_pin: ^!P0.28
contrast: 63

[output_pin beeper]
pin: EXP1_1

[neopixel fysetc_mini12864]
pin: EXP1_6
chain_count: 3
color_order: RGB
initial_RED: 0.0
initial_GREEN: 0.2
initial_BLUE: 0.0

##  Set RGB values on boot up for each Neopixel.
##  Index 1 = display, Index 2 and 3 = Knob
[delayed_gcode setdisplayneopixel]
initial_duration: 1
gcode:
        SET_LED LED=fysetc_mini12864 RED=0 GREEN=0 BLUE=1 INDEX=1 TRANSMIT=0
        SET_LED LED=fysetc_mini12864 RED=0 GREEN=1 BLUE=0 INDEX=2 TRANSMIT=0
        SET_LED LED=fysetc_mini12864 RED=0 GREEN=1 BLUE=0 INDEX=3**

after restarting have got this message

**mcu 'mcu': Unable to encode: config_spi

This type of error is frequently caused by running an older
version of the firmware on the micro-controller (fix by
recompiling and flashing the firmware).

Known versions: host=v0.10.0-278-g7c964e5f, mcu=v0.10.0-419-g4490a584, rpi=v0.10.0-278-g7c964e5f

Once the underlying issue is corrected, use the "RESTART"
command to reload the config and restart the host software.
Protocol error connecting to printer**

if i comments the display section - the mcu starts but there is no any data on display only light on

so if anyone could help me will be appreciated!
thank you

mitofun, 2022-06-21:
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

mitofun, 2022-06-21:
have managed to start it! yep need to remove the R1 and C6 (the cables good no need to change anything!)
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
all you need to upgrade the klipper and the moonraker!
the code i have used as the following

#############################################
## BOARD PINS + DISPLAY + SD CARD
#############################################
######################################################################
# BTT SKR 1.4 Turbo
######################################################################
[board_pins]
aliases:
    # EXP1 header
    EXP1_1=P1.30, EXP1_3=P1.18, EXP1_5=P1.20, EXP1_7=P1.22, EXP1_9=<GND>,
    EXP1_2=P0.28, EXP1_4=P1.19, EXP1_6=P1.21, EXP1_8=P1.23, EXP1_10=<5V>,
    # EXP2 header
    EXP2_1=P0.17, EXP2_3=P3.26, EXP2_5=P3.25, EXP2_7=P1.31, EXP2_9=<GND>,
    EXP2_2=P0.15, EXP2_4=P0.16, EXP2_6=P0.18, EXP2_8=<RST>, EXP2_10=<NC>
    # Pins EXP2_1, EXP2_6, EXP2_2 are also MISO, MOSI, SCK of bus "ssp0"
######################################################################
# Fysetc Mini 12864Panel v2.1 (with neopixel backlight leds)
######################################################################
[display]
lcd_type: uc1701
cs_pin: EXP1_3
a0_pin: EXP1_4
rst_pin: EXP1_5
contrast: 63
encoder_pins: ^EXP2_5, ^EXP2_3
click_pin: ^!EXP1_2
contrast: 63
## Some micro-controller boards may require an spi bus to be specified:
#spi_bus: spi
## Alternatively, some micro-controller boards may work with software spi:
#spi_software_miso_pin: EXP2_1
#spi_software_mosi_pin: EXP2_6
#spi_software_sclk_pin: EXP2_2
[output_pin beeper]
pin: EXP1_1
[neopixel fysetc_mini12864]
pin: EXP1_6
chain_count: 3
initial_RED: 0.2
initial_GREEN: 0.2
initial_BLUE: 0.0
#initial_RED: 0.4
#initial_GREEN: 0.4
#initial_BLUE: 0.4
color_order: RGB
# For Mainsail and Fluidd
#############################################
[display_status]
# for display messages in status panel
#############################################
[pause_resume]
recover_velocity: 50
# for pause/resume functionality.
# Mainsail needs gcode macros for `PAUSE`, `RESUME` and `CANCEL_PRINT` to make the buttons work.
######################################################################
# Plug pin locations
######################################################################

# Some micro-controller boards and displays use inconsistent labeling
# for the EXP1 and EXP2 headers. The following diagram shows the
# correct location of pin 1 along with ground and power pins on the
# EXP1 and EXP2 plugs:
#
#          EXP1:                        EXP2:
#   +-----------------+          +-----------------+
#   |  o  o  o  o  5V |          |  o  o  o  o  o  |
#   |  1  o  o  o GND |          |  1  o  o  o GND |
#   +------     ------+          +------     ------+
#
# Some boards may have the cutout in the wrong location. If so, it may
# be possible to carefully pry the plastic header off of the pins with
# a small screwdriver, then correct the orientation and reapply the
# plastic header.
######################################################################
# SET DISPLAY NEOPIXEL
######################################################################
[delayed_gcode setdisplayneopixel]
initial_duration: 1
gcode:
#        SET_LED LED=fysetc_mini12864 RED=1 GREEN=1 BLUE=1 INDEX=1
#        SET_LED LED=fysetc_mini12864 RED=1 GREEN=0 BLUE=0 INDEX=2
#        SET_LED LED=fysetc_mini12864 RED=1 GREEN=0 BLUE=0 INDEX=3 TRANSMIT=0

        SET_LED LED=fysetc_mini12864 RED=0 GREEN=1 BLUE=0 INDEX=1 TRANSMIT=0
        SET_LED LED=fysetc_mini12864 RED=0 GREEN=1 BLUE=0 INDEX=2 TRANSMIT=0
        SET_LED LED=fysetc_mini12864 RED=1 GREEN=1 BLUE=0 INDEX=3

raymondh2, 2022-06-21:
Most of the people who will be able to help you are on our reddit and discord. I'd suggest going to the Vorondesign.com website and going there.

Closed 2022-06-21.

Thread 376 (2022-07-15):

Cable chain retainer brackets - how is this meant to work?

Alex9779, 2022-07-15:
I overhauled my Voron 2.4 with some of the 2.4 R2 parts because of some issues and a switch to the Stealthburner.
But I do not get how the cable chain retainers should work, mentioned on page 232 of the manual. I have to use those because I changed my A/B drive units too, the original parts I ordered from a print-it-forward turned out to be a little off.
I printed the chable chain retainer brackets to fix my generic three hole cable chain but the hole of the retainer is about 4mm in diameter, an M5 screw will sit tight but is too big for the cable chain holes.
The M3x10 FHCS of the manual just slides through and there is nothing it screws into so.
For the moment I used a hex nut, but I don't think this is the way it should be...

Is there something missing? Is the hole of the retainer too big?

Or did I miss something?

DunarDolorgiet, 2022-07-17:
Have a look at page 231, the updated ones use heat set inserts instead of hexnuts.
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

Alex9779, 2022-07-17:
Ahhh cool, sorry I missed that... Thanks!

Closed 2022-07-17.

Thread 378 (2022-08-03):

Manual Specifies wrong wire thickness.

neeamradia, 2022-08-03:
Page 210 of the 2.4r2 manual specifies:

'Cables should be at least 1mm^2 (AWG18) or thicker depending on local regulations.'

18AWG = 0.75mm^2
0.1mm^2 = 16AWG?

Which one should it be? 18 or 16 AWG?

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

nemgrea, 2022-08-05:
American 18 gauge wire is listed at 0.0403in diameter which is above 1mm. where are you getting .75mm from?

neeamradia, 2022-08-06:
> American 18 gauge wire is listed at 0.0403in diameter which is above 1mm. where are you getting .75mm from?
>
> EDIT: i believe you may be looking at cross sectional area of which it would be closer to 0.75 when what is called out in the note is thickness (i.e. diameter)

Sorry - yes that is likely that I am looking at the wrong dimension.

Closed 2022-08-05.

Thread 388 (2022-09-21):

[Manual] Mention that Hall Effect PCB is for legacy support and not in any way an upgrade

ChaosBlades, 2022-09-21:
In the manual the Hall Effect is presented as an upgrade. At least I interpreted it that way and it seems several people in the Amazon reviews for the Hall Effect PCB I bought thought this as well. Turns out the Hall Effect sensor is worse in basically every way from the micro switches as I found out asking about it in Discord. This should really be pointed out in the documentation or just removed from the manual all together.

raymondh2, 2022-09-22:
I'll bring it up to the team.

nemgrea, 2022-09-22:
> In the manual the Hall Effect is presented as an upgrade. At least I interpreted it that way and it seems several people in the Amazon reviews for the Hall Effect PCB I bought thought this as well.

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

its shown as an option, i dont think there is anything in here that expresses that one is better than the other or that one would be an upgrade over the other, simply two options are shown.

ChaosBlades, 2022-09-22:
I don't think that is good enough. According to my discussion on Discord the hall effect isn't any more reliable than micro switches, it is sensitive to chamber temp, switching to PLA when tuned for ABS it could go so out of spec enough to cause a crash, it drifts over time, and you can't even increase home speed. It is not an improvement in any way.

What I was told was...

> StevenB V2.3370 — Yesterday at 2:55 AM
Because it was a test that failed and it's still kept as an option because of that.

When I go to some of these selling on Amazon I see people complaining that the Hall Effect PCBs are using a different connector (Molex instead of JST) so they need to re-cable when moving from Microswitch. Which is a downgrade. So clearly myself and other have fallen victim to this simply being show as an option. I am sure there is some kind of lesson here on assuming things.

nemgrea, 2022-09-22:
i agree is is not any more reliable at all NOR is it ever claimed to be more reliable, im not sure why you are assuming that it would be more reliable when it is not presented as "better" or of higher quality in any of the documentation. it is simply showing steps for an OPTION that exists and happens to be popular. no claims of its benefits or performance are shown stated or implied in the manual...

subatomicglue, 2022-09-23:
I wonder if OP is getting at:
 - Shouldn't the default of voron's manual be to clearly highlight the
"best", for the optimal voron experience?   Like, If I'm presented with 2
options, and I know not which is better, shouldn't there be something
helping guide me to choose, so that I make the best voron printer available
and not go down "less-good" paths?

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

raymondh2, 2022-09-23:
Our BOM already lists the normal microswitch setup and not any of the PCBs. But these PCBs are included in the manual because they are so common and we get too many questions when we don't include the instructions for it.

asdasdwa-v02679, 2023-05-30:
Could we possibly solve this problem by adding text on page 191 below the images that has a warning specifying that although the pcbs can simplify wiring they tend to introduce their own issues with repeatability and aren't recommended.

or is it just the hall effect pcb? if so perhaps it would read more like "although the hall effect sensor pcbs have become super common and can simplify wiring, they tend to introduce their own issues with repeatability and aren't recommended."

does this seem like a good solution according to yall? if so and people approve I am happy to make the edit to the page :)

asdasdwa-v02679, 2023-06-10:
@majarspeed  I understand that but It seems that Nemgrea marked it as manual so I was trying to find a solution. also It does seem a fair few people get confused by this page and so a edit might be in order ?

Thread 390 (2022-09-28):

Manual for Z axis missing Z idler assembly + suggestion for manual.

Eclypse3D, 2022-09-28:
In the manual while going though the parts, on page 109 for Z axis it shows Z idler at the top of the gantry, it then again references the Z idler on page 117 just before the belt install, but nowhere is the page on the assembly of the Z idler.  No mention what or how many bolts, nuts, or anything hardware related is mentioned, it only mentions extending the idler during the belt install.  Needs update and clarity.

Suggestion for the manual over all. On each section of the build just after the cad drawing, on the overview page, it would be prudent to include the parts list for each section.  i.e. z idler x4, M3x20 x8, M3 nut x1 etc.  For each section.  This would help the builders consolidate parts in a compartmentalized fashion.

julianschill, 2022-09-28:
Z Idler assembly is on page 48 - 50.

Not sure about the part list. On the one side it would be nice, on the other side it would be a lot of work to do and is more like a "nice to have" than a necessity. And it would be quite a lot of work to prepare.

Eclypse3D, 2022-09-28:
Oh jeese how did I blast past those pages, I think maybe the browser skipped over it while scrolling I was going through the parts I had printed to inventory from the manual and never saw those pages, well nvm then....

As far as the manual thing, how much harder would it be? the time was taken to make the manual, and create a bom.  I am not sure that is a is a stretch considering the work already done.  If anything, it seems like it was more of an oversight as most other  manuals usually give you some sort of parts list.  Yes we have a bom, and technically that with the manual would be a rough equivalent, but its not a replacement.  Yeah it would be nice to see at least future manuals with it during creation.

Eclypse3D, 2022-09-28:
Pages found, false alarm...

Closed 2022-09-28.

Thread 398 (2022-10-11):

[Manual] Z drive assembly doesn't mention seating set screws on motor shaft

loopj, 2022-10-11:
Hey folks, absolutely love the manual but wanted to share something I missed on my initial build which could be an opportunity to improve it even further.

For the extruder and belt drive assembly there is a note that says:
> Make sure the set screw in the drive pinion is seated on the flat of the motor shaft.

I think it would be great to say the same thing on page 38 for attaching the pulley to the Z drive shafts.

asdasdwa-v02679, 2023-05-17:
I think this edit resolves the suggestion. let me know if you meant something different! just in case it does resolve it as is, here is a updated version of the page plus a higher rez of just the edited assembly for the convenience of the Manual team!
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

Closed 2024-02-09.

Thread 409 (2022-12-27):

V2.4 part cooling fan causing VFA's

jhenley01, 2022-12-27:
Hello everybody. I wanted to share something I've found regarding VFA's in case it helps anyone else who is having the issue. I recently built a LDO kit V2.4 and have been very happy with printer. I decided to upgrade from CW1 to CW2 and immediately started seeing VFA's on my prints. I print with black PETG a lot and being so shiny it really highlights imperfections in the print surface.

I went down the usual rabbit hole of trying to solve the VFA issue. I checked belts, tightened every screw, tuned motor currents, changed microstepping, changed from the dual gear extruder to single gear with idler bearing, checked wiring, even swapped out the LDO extruder motor for a Moons. Nothing made any difference.

Then on one of my random test prints I noticed that the VFA issue had greatly improved. What changed? I had increased the part cooling fan from the usual 30% to 50%. I then did another test at 0% part cooling fan and it was even better!

An interesting note is that I was still using Stealthburner with my CW1 setup so there wasn't much change to the part cooling fan setup. I used the same SB parts and only added the 2 piece CW2 PCB. Since one of the PCBs sits on top of the part cooling fan there may be some vibration there now but still interesting that the artifacts lessen with higher fan speeds.

I've attached a few photos of test prints, the only change is the part cooling fan speed. I also did a test with the fan starting at 0% and increasing 10% every 5mm. For whatever reason it really doesn't like the fan running in the 30-40% range. I'll probably try replacing the fan to see if that changes anything. It's hard to get good pictures of the issue but in person the change is dramatic.

I've seen a lot of posts about VFA's but haven't seen any that mentioned the part cooling fan. I know there are lots of things that can cause print artifacts but if you're having issues with them it may be worth looking at the part cooling fan.

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

nemgrea, 2022-12-27:
VFA's are most commonly caused by resonance in your printer so changing something like a fan speed can cause that resonance frequency to shift and improve or worsen the effect. changing printing speeds can also show changes in VFA's the goal is to get your setup such that the frequency of vibration of your machine do NOT match its resonance frequency and then you will not have VFA's

raymondh2, 2022-12-28:
This would do better in a discussion on our forum. https://forum.vorondesign.com/

Closed 2022-12-28.

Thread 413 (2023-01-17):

Y-Axis Gantry Page - 89

KingVeder, 2023-01-17:
Minor but the screw/T-Nut on the rail should start on the second one in, on both sides to allow for the Idler M3 & M5 T-Nut
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

nemgrea, 2023-01-18:
if the directions on page 88 are followed all of the T-nuts fit properly as shown.

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

newphreak, 2023-01-18:
This is very much a real issue on 300mm builds. I forget the math, but i think the 50mm difference from the 300 and 400mm rails is what makes the 300 (350mm rail) have less space here.

andreasbeh, 2023-03-28:
Can confirm this issue exists on a 300mm build, I am about 5mm short each end from being able to fit a M5 ball-spring nut. It fits just fine with a slide-in style nut, though that needs double checking for a 250mm build.
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

asdasdwa-v02679, 2023-05-30:
hello freinds, I hope this edit solves the problem :) let me know if it needs to be changed!

 full page : 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

edited parts:
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

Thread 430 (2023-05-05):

T-Nut not fitting - Manual page 90

miracuruzrh, 2023-05-05:
Hi

I ordered from a chinese seller a kit for the Voron 2.4 350mm version.
In the manual there is a problem at page 90 -93 where the Front idlers / Z-Joint should be assembled with the T-Nuts.
The mentioned T-Nuts can't be installed this way, because the M3x8 screw and T-Nut from the MGN9 Linear rail is blocking the nut already.
The only way to install both T-Nuts was for me to turn them 180° and cut the outer T-Nut in half so that it did not overlap.
I have made a drawing which shows the problem, where T-Nut 1 and T-Nut 2 are overlapping.

Now is my question. Should this be mentioned in the manual, or did I something wrong for the 350mm version?
[Voron r2.4.pdf](https://github.com/VoronDesign/Voron-2/files/11408300/Voron.r2.4.pdf)

Here I have just added my workaround
[Voron r2.4 Workaround.pdf](https://github.com/VoronDesign/Voron-2/files/11408596/Voron.r2.4.Workaround.pdf)

nemgrea, 2023-05-06:
duplicate issue
#413

Closed 2023-05-06.

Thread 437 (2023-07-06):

Voron Trident and 2.4 not working with soft material

Ziiiwei, 2023-07-06:
I have built both with klicky probe and bed-atached z-endstop. Althought they work well with abs and all the other hard materials, they really sucked with soft TPU in my settings. The main issue is with the soft material geting streched and stuck in the PTFE tube. Both machine are driect drive design yet still heavily rely on long PTFE tube for the filment guidance. Pulling soft material through tube(especially with that 90 degree turn in back of printer) gonna create a lots of resistance, and as the material get streched and therefore thiner, the gear grip also decreace. Both machine are guaranteed to stuck after about 20 min run as the streching build up. Currently i have to open the top cover and put spool holder up in the top to get rid off the PTFE tube to make is print smoothly(the direct drive ender3 set up). Does anyone have similar issues and have already worked out a more elegant solution?
Another difficulty is I have to clean the z-endstop before the z-calibration when homing leaves sticky soft TPU on the stwich, otherwise I may have the print head diging into the bed. I'm currently trying switching to voron tap to solve this, but that will have potential conflicts with above tube less set up(as the print head move around pulling the fillament, if might just pull up the print head and trigger the switch).
I'm guessing the way to actually solve this to have a separate drive at begining of the tube? But that really feels like a over kill, so anyone having this issue please help with my frustration...

valadas, 2023-07-06:
What I do for tpu is that I leave the doors open and remove the tube. I mount the spool top front and just feed the toolhead direct without any tube.

photodave, 2023-08-31:
I have had my V2.4 350mm for a little over a year and have printed several items with TPU from Polymaker, Duramic 3D and Eryone, with no failed prints with any of the TPU spools I tried. Im using the CW2 extruder and have my spool holder mounted on the outside rear right so the base of the spool is about 1" above the top of the skirts. I did mod the "bowden_retainer.stl" and extend it so when mounted above the spool, the bowden tube would line up roughly with the outside edge of the spool so it would also make a more gentle arc when going into the enclosure. Anyway I just thought I would throw that out there as I have not had any problems with various spools of TPU.

Closed 2024-02-09.

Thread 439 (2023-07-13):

Manual: Z Idler

1John419, 2023-07-13:
On page 48, the GT2 20 Tooth Idler is shown fixed by a M5x30 BHCS screw.

Although not explicitly stated, I had assumed that it was screwed directly into the plastic of the Z Tensioner. However, printed part has no retention on the screw and the STL clearly shows a through 5.0mm diameter hole. As I measure a typical M5 at 4.75mm diameter, this appears to be an intention slip fit.

My only guess is that the design intends to utilize belt tension to retain the screw. If that is true, as a first build, this is a very confusing omission of information.

I have suspended my build until there is clarification of design intent.

ensoniq2k, 2023-07-14:
It's screwed directly into plastic. In my case I didn't even notice because of warping of the ASA the hole needed to be drilled out anyway.

nemgrea, 2023-07-14:
> As I measure a typical M5 at 4.75mm

4.75mm is out of din spec for the major diameter of an m5 bolt.

1John419, 2023-07-14:
Yes, I have confirmed that some of the Formbot kit fasteners are out of spec. I have some other M5 fasteners that are in spec (4.86mm diameter) which do produce a very slight bite when threaded. I'll order some new fasteners (confirming their spec), reprint the parts, and see if that yields the desired results.

As a first time builder, I would comment that the manual could be clearer regarding this matter. Other threaded directly into plastic parts (e.g., A/B Drive and XY Joint) have printed in place threads. For the Z Idlers, perhaps making these mirrored parts with printed in place threads on the outward arms (and slightly oversized hole on the inward arms) would provide a better solution.

1John419, 2023-07-17:
OK. Got some in spec fasteners (4.96mm). Reprinted parts. Fastener bites into part allowing a slight torqueing and solid retention. Build restarted.

Opened a ticket with Formbot to report the issue with fasteners.

Closed 2023-07-17.

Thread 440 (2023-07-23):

Need Help with quad gantry

christofeugster, 2023-07-23:
Hi guys.
I have a voron 24 for over 3 Years now. All fine unless the Bed Level is broken.
Ive tried everything.
The Bed tilts visually down towards Y 350, but Bed-Mesh shows oposite.
My first Layer normally PLA are just holding. But now im with PVA. and the prints gets loose.
It seams that Quad Gantry level does not level. Or i assume, Y Axis is somehow inverted when the correction happens.
Bed_Mesh makes things worse.
Im working with klipper, fluidd, moonraker with a Fystec 1.0 Motorcontroller. Slicer (Cura or Prusa, same Outcome)
-When doing a Bed_Mesh calibrate, the outcome is verry similar with a deviation of around 0.16 !!!The Bed is evenly tilted upwards to Y 350!!!
-After Quad Gantry Level i can see, that the gantry is not level on Y Axis !!!

What i think could be the Problem.
1. When Bed_Mesh - changes in Y axis are inverted and make the Problem worse.
2. Stepper Motors 17hs19  2004S1 do only 0.1mm steps everything in between is rounded up or down.
3. Bed_Mesh Profile is not used, even when explicit load one
4. Somewhere is a Mesh profile that loads. I had issues with path finding. Made the path fix mod!

If somebody can help me, would be great. Thanks!

print.cfg:
# This file contains common pin mappings for the Fysetc Spider board.
# To use this config, the firmware should be compiled for the STM32F446.
# When calling "menuconfig", enable "extra low-level configuration setup"
# and select the "12MHz crystal" as clock reference
# For flashing, write the compiled klipper.bin to memory location 0x08000000

# See docs/Config_Reference.md for a description of parameters.

## Voron Design VORON2 250/300/350mm Spider TMC2209 UART config

## *** THINGS TO CHANGE/CHECK: ***
## MCU paths							[mcu] section
## Thermistor types						[extruder] and [heater_bed] sections - See 'sensor types' list at end of file
## Z Endstop Switch location			[safe_z_home] section
## Homing end position				[gcode_macro G32] section
## Z Endstop Switch  offset for Z0		[stepper_z] section
## Probe points							[quad_gantry_level] section
## Min & Max gantry corner postions		[quad_gantry_level] section
## PID tune								[extruder] and [heater_bed] sections
## Fine tune E steps					[extruder] section

[mcu]
## Uncomment below if you're using the Raspberry uart0 to communicate with Spider
#restart_method: command

##  You need to select 'Communication interface' to USB in 'make menuconfig'
##  when you compile Klipper for Spider
##	Obtain definition by "ls -l /dev/serial/by-id/" then unplug to verify
##--------------------------------------------------------------------
serial: /dev/serial/by-id/usb-Klipper_stm32f446xx_270047000350305538333620-if00
##	If you want to use the Raspberry uart0 to communicate with Spider,
##  you need to select 'Communication interface' to 'Serial (on USART1 PA10/PA9)'
##  in 'make menuconfig' when you compile klipper and set the serial as below
##--------------------------------------------------------------------
#serial: /dev/ttyAMA0
##--------------------------------------------------------------------

[printer]
kinematics: corexy
max_velocity: 300
max_accel: 3000			        #Max 4000
max_z_velocity: 15			#Max 15 for 12V TMC Drivers, can increase for 24V
max_z_accel: 350
square_corner_velocity: 5.0

#####################################################################
#      X/Y Stepper Settings
#####################################################################

[stepper_x]
##	Connected to X-MOT (B Motor)
step_pin: PE11
dir_pin: !PE10
enable_pin: !PE9
rotation_distance: 40
microsteps: 16
full_steps_per_rotation:200  #set to 400 for 0.9 degree stepper
endstop_pin: ^PA1 #PB14
position_min: 0

##--------------------------------------------------------------------

##	Uncomment for 350mm build
position_endstop: 350
position_max: 350

##--------------------------------------------------------------------
homing_speed: 25   #Max 100
homing_retract_dist: 5
homing_positive_dir: true

##	Make sure to update below for your relevant driver (2208 or 2209)
[tmc2209 stepper_x]
uart_pin: PE7
interpolate: True
run_current: 0.7
hold_current: 0.4
sense_resistor: 0.110
stealthchop_threshold: 0

[stepper_y]
##	Connected to Y-MOT (A Motor)
step_pin: PD8
dir_pin: !PB12
enable_pin: !PD9
rotation_distance: 40
microsteps: 16
full_steps_per_rotation:200  #set to 400 for 0.9 degree stepper
endstop_pin: PB13
position_min: 0
##--------------------------------------------------------------------

##	Uncomment for 350mm build
position_endstop: 350
position_max: 350

##--------------------------------------------------------------------
homing_speed: 25  #Max 100
homing_retract_dist: 5
homing_positive_dir: true

##	Make sure to update below for your relevant driver (2208 or 2209)
[tmc2209 stepper_y]
uart_pin: PE15
interpolate: True
run_current: 0.7
hold_current: 0.4
sense_resistor: 0.110
stealthchop_threshold: 0

#####################################################################
#   Z Stepper Settings
#####################################################################

## In Z-MOT Position
## Z0 Stepper - Front Left
[stepper_z]
step_pin: PD14
dir_pin: !PD13
enable_pin: !PD15
rotation_distance: 40
gear_ratio: 80:16
microsteps: 16
##  In Z- Position
endstop_pin: ^PA0
##  Z-position of nozzle (in mm) to z-endstop trigger point relative to print surface (Z0)
##  (+) value = endstop above Z0, (-) value = endstop below
##	Increasing position_endstop brings nozzle closer to the bed
##  After you run Z_ENDSTOP_CALIBRATE, position_endstop will be stored at the very end of your config
#position_endstop: -0.5
##--------------------------------------------------------------------

##	Uncomment below for 350mm build
position_max: 340

##--------------------------------------------------------------------
position_min: -5
homing_speed: 8
second_homing_speed: 3
homing_retract_dist: 3

##	Make sure to update below for your relevant driver (2208 or 2209)
[tmc2209 stepper_z]
uart_pin: PD10
uart_address: 0
interpolate: True
run_current: 0.7
hold_current: 0.4
sense_resistor: 0.110
stealthchop_threshold: 0

##	In E1-MOT Position
##	Z1 Stepper - Rear Left
[stepper_z1]
step_pin: PE6
dir_pin: PC13
enable_pin: !PE5
rotation_distance: 40
gear_ratio: 80:16
microsteps: 16

##	Make sure to update below for your relevant driver (2208 or 2209)
[tmc2209 stepper_z1]
uart_pin: PC14
interpolate: True
run_current: 0.7
hold_current: 0.4
sense_resistor: 0.110
stealthchop_threshold: 0

##	In E2-MOT Position
##	Z2 Stepper - Rear Right
[stepper_z2]
step_pin: PE2
dir_pin: !PE4
enable_pin: !PE3
rotation_distance: 40
gear_ratio: 80:16
microsteps: 16

##	Make sure to update below for your relevant driver (2208 or 2209)
[tmc2209 stepper_z2]
uart_pin: PC15
interpolate: true
run_current: 0.7
hold_current: 0.4
sense_resistor: 0.110
stealthchop_threshold: 0

##	In E3-MOT Position
##	Z3 Stepper - Front Right
[stepper_z3]
step_pin: PD12
dir_pin: PC4
enable_pin: !PE8
rotation_distance: 40
gear_ratio: 80:16
microsteps: 16

[tmc2209 stepper_z3]
uart_pin: PA15
interpolate: true
run_current: 0.7
hold_current: 0.4
sense_resistor: 0.110
stealthchop_threshold: 0

#####################################################################
#   Extruder
#####################################################################

##	In E0-MOT Position
[extruder]
step_pin: PD5
dir_pin: !PD6
enable_pin: !PD4

##	Update value below when you perform extruder calibration
##	If you ask for 100mm of filament, but in reality it is 98mm:
##	rotation_distance = <previous_rotation_distance> * <actual_extrude_distance> / 100
##  22.6789511 is a good starting point
rotation_distance: 22.6789511	#Bondtech 5mm Drive Gears
##	Update Gear Ratio depending on your Extruder Type
##	Use 50:17 for Afterburner/Clockwork (BMG Gear Ratio)
##	Use 80:20 for M4, M3.1
gear_ratio: 50:17				#BMG Gear Ratio
microsteps: 16
full_steps_per_rotation: 200	#200 for 1.8 degree, 400 for 0.9 degree
nozzle_diameter: 0.400
filament_diameter: 1.75
##      In E0 OUT Position
heater_pin: PB15
##	Validate the following thermistor type to make sure it is correct
sensor_type: Generic 3950 #ATC Semitec 104GT-2
sensor_pin: PC0 # TE0 Position
min_temp: 10
max_temp: 270
max_power: 1.0
min_extrude_temp: 170
control = pid #--> aktiviert
pid_kp = 26.213  #--> aktiviert
pid_ki = 1.304  #--> aktiviert
pid_kd = 131.721  #--> aktiviert
##	Try to keep pressure_advance below 1.0
pressure_advance: 0.05
##	Default is 0.040, leave stock
pressure_advance_smooth_time: 0.040

##	In E0-MOT Position
##	Make sure to update below for your relevant driver (2208 or 2209)
[tmc2209 extruder]
uart_pin: PD7
interpolate: false
run_current: 0.5
hold_current: 0.2
sense_resistor: 0.110
stealthchop_threshold: 0

#####################################################################
#   Bed Heater
#####################################################################
[heater_bed]
##	SSR Pin - In BED OUT position
heater_pin: PB4
sensor_type: Generic 3950 ## NTC 100K beta 3950
sensor_pin: PC3 # TB Position
##	Adjust Max Power so your heater doesn't warp your bed
### max_power from 0.6 to 0.8
max_power: 0.8
min_temp: 0
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
nemgrea, 2023-07-28:
help requests should be direct to the help channels on discord or the proper sections on the voron Forum

this is for issues with items in the git repos

Closed 2023-07-28.

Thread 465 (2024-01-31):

X Carriage Frames and Manual/STL Discrepancies

nilchaos, 2024-01-31:
The Voron2 assembly manual (page 129) linked on the website shows an image of the X carriage for the Afterburner/CW1 where the SHCS is screwed in from the back.

The Stealthburner/CW2 manual (page 58) shows a different X carriage where there are two heat set inserts at the top of the frames.

If downloading the Voron2 STLs from the website, the bundled zip on the r2 release page contains the Afterburner/CW1 X carriage frames without the ability to mount the top two heat set inserts.

Manually drilling into the Voron2 STL repo folder or using the CLICK HERE TO DOWNLOAD link in the repo readme has the correct x carriage frames but if people don't know better and download the bundled zip in the r2 release post containing the old ones they will run into this problem during assembly.

nilchaos, 2024-01-31:
Didn't notice the other issue addressing this - #444

Closed 2024-01-31.

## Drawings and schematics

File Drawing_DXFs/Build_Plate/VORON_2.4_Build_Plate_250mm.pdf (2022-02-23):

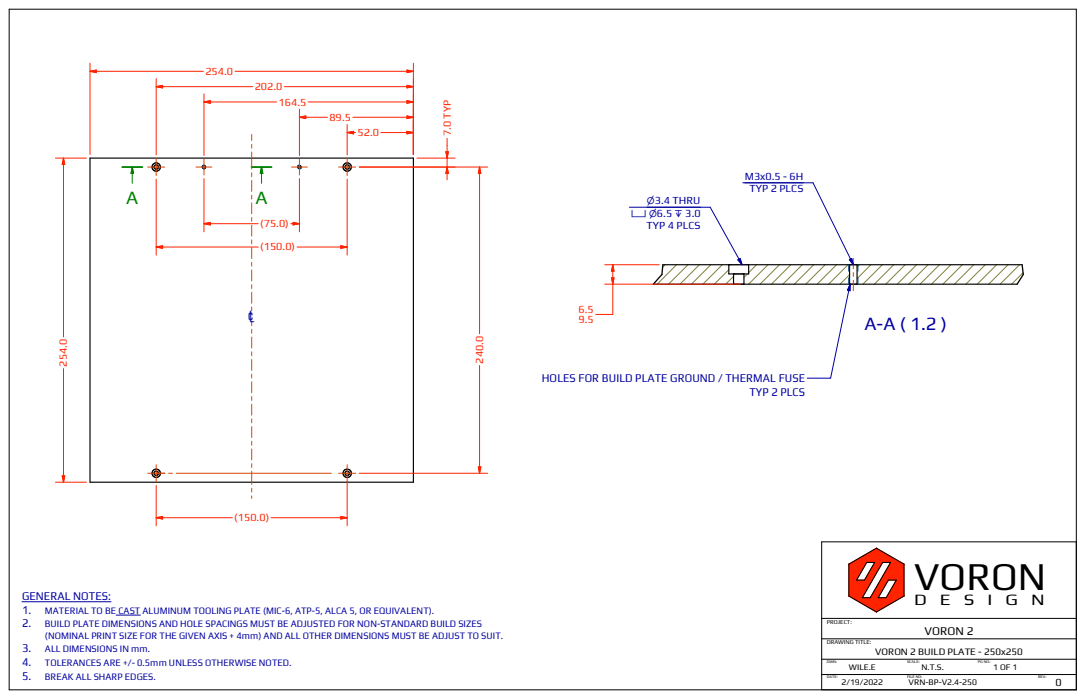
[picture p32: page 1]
VRN-BP-V2.4-250 DATE:; FILE NO:; PROJECT: DRAWING TITLE:; VORON 2; VORON 2 BUILD PLATE - 250x250 DWN:; SCALE:; PG NO: WILE.E; VORON; REV:; 164.5 240.0 7.0 TYP; TYP 2 PLCS; n3.4 THRU v n6.5 x 3.0 TYP 4 PLCS; M3x0.5 - 6H TYP 2 PLCS

HOLES FOR BUILD PLATE GROUND / THERMAL FUSE

GENERAL NOTES:
1. MATERIAL TO BE CAST ALUMINUM TOOLING PLATE (MIC-6, ATP-5, ALCA 5, OR EQUIVALENT).
2. BUILD PLATE DIMENSIONS AND HOLE SPACINGS MUST BE ADJUSTED FOR NON-STANDARD BUILD SIZES
(NOMINAL PRINT SIZE FOR THE GIVEN AXIS + 4mm) AND ALL OTHER DIMENSIONS MUST BE ADJUST TO SUIT.
3. ALL DIMENSIONS IN mm.
4. TOLERANCES ARE +/- 0.5mm UNLESS OTHERWISE NOTED.
5. BREAK ALL SHARP EDGES.

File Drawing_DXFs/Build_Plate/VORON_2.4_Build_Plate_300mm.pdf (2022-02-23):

A A

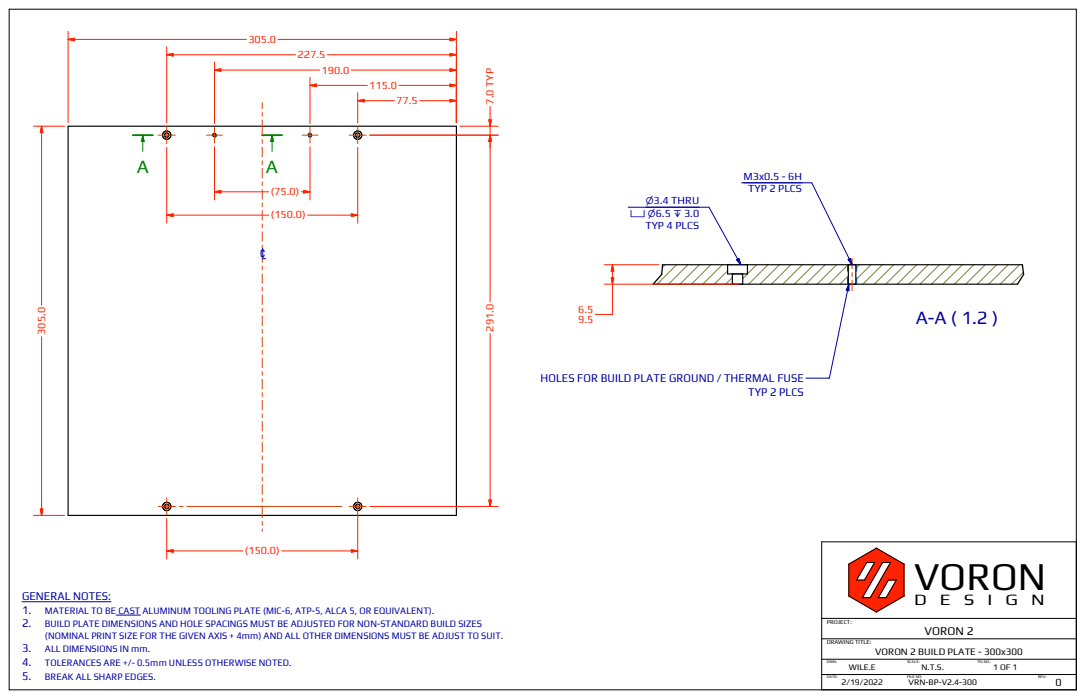
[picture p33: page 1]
VRN-BP-V2.4-300 DATE:; FILE NO:; PROJECT: DRAWING TITLE:; VORON 2; VORON 2 BUILD PLATE - 300x300 DWN:; SCALE:; PG NO: WILE.E; VORON; REV:; 190.0 291.0 7.0 TYP; TYP 2 PLCS; n3.4 THRU vn6.5 x 3.0 TYP 4 PLCS; M3x0.5 - 6H (75.0) TYP 2 PLCS

HOLES FOR BUILD PLATE GROUND / THERMAL FUSE

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

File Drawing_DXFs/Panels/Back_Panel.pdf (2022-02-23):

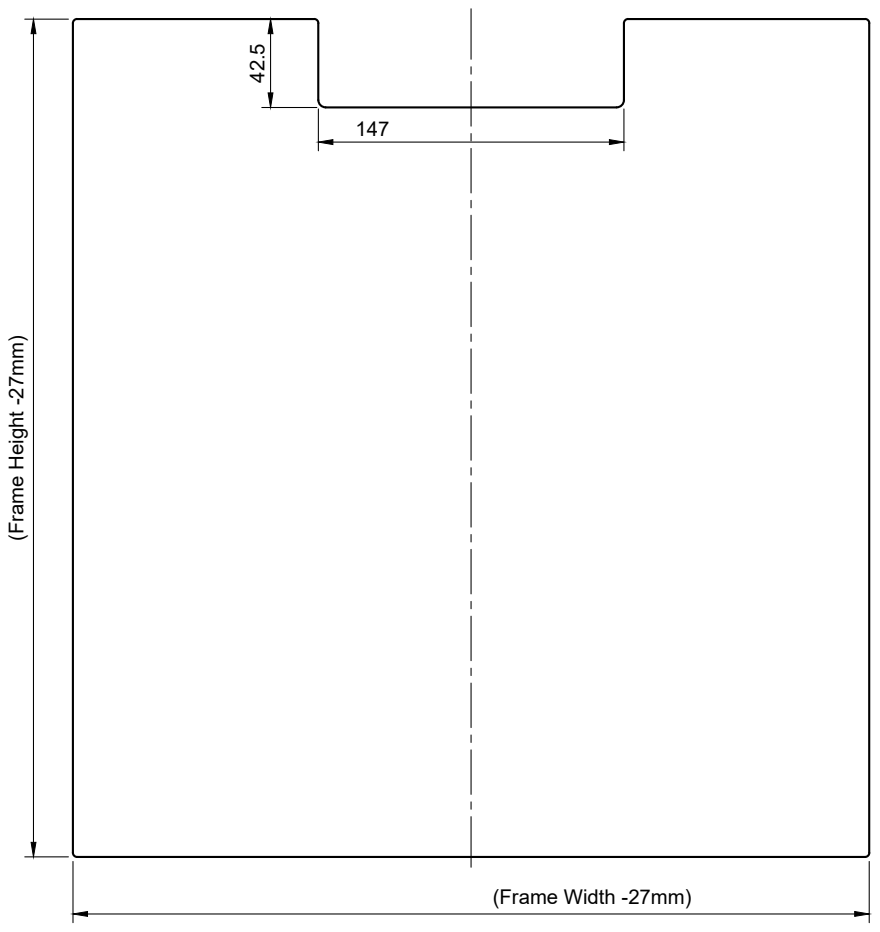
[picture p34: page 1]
147 42.5 (Frame Height -27mm); (Frame Width -27mm)

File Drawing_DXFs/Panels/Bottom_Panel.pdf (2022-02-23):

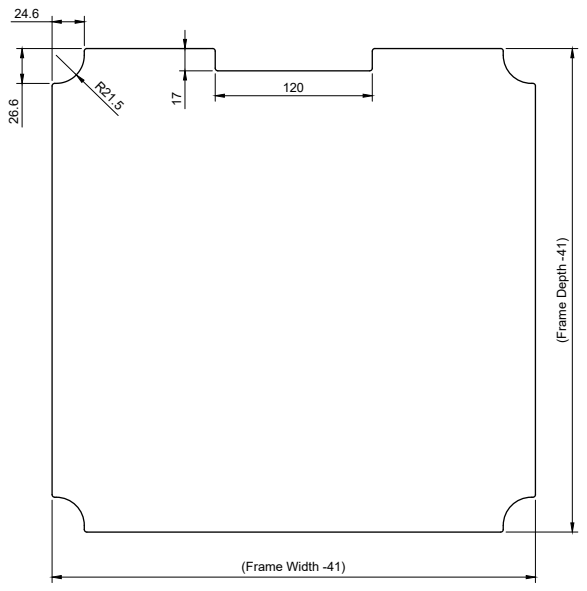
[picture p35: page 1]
(Frame Width -41); (Frame Depth -41)

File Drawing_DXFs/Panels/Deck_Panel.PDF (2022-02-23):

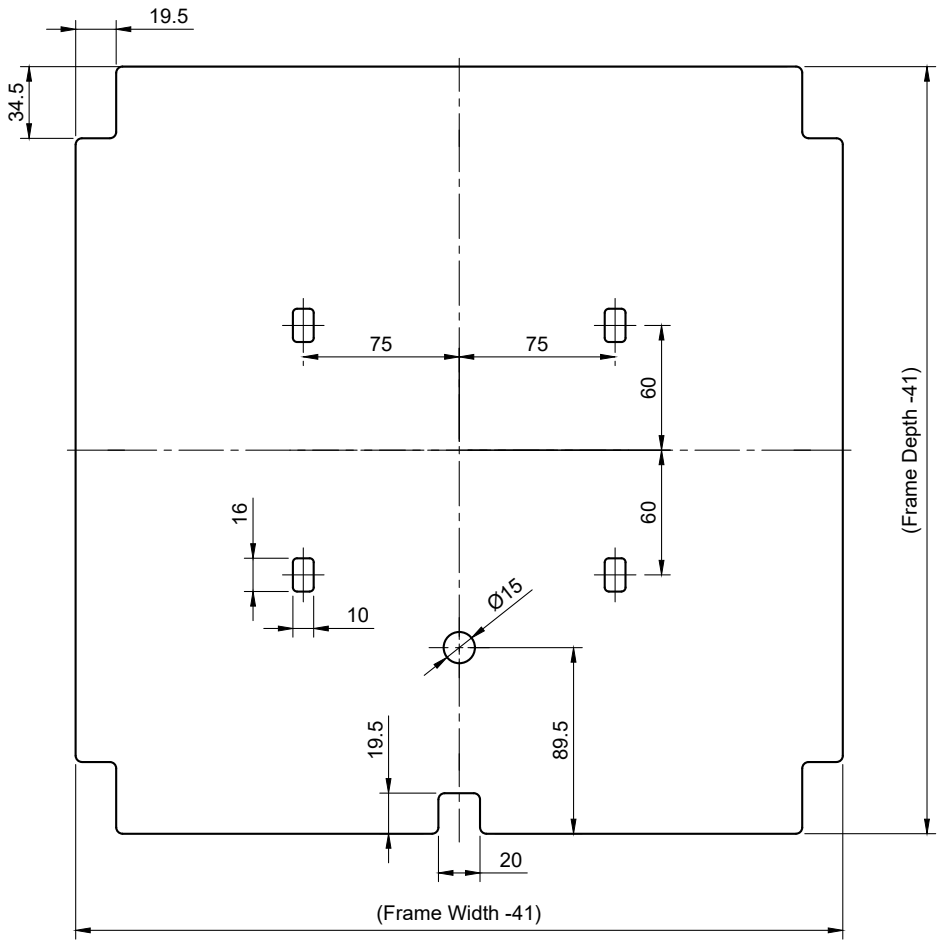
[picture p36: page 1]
(Frame Width -41); (Frame Depth -41)

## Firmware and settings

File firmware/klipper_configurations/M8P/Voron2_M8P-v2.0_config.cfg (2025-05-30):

# This file contains common pin mappings for the BIGTREETECH Manta M8P V2.0
# To use this config, the firmware should be compiled for the
# STM32H723 with a "8KiB bootloader" and USB communication.

# This config is currently only correct for V2.0 boards
# 
# See docs/Config_Reference.md for a description of parameters.

[mcu]
##	[X in MOTOR1] - B Motor
##	[Y in MOTOR2] - A Motor
##	[E in MOTOR8] - Extruder
##	Obtain definition by "ls /dev/serial/by-id/*" then unplug to verify
##--------------------------------------------------------------------
serial: /dev/serial/by-id/YOU_DIDNT_CHANGE_ME_YET
#restart_method: command
##--------------------------------------------------------------------

[printer]
kinematics: corexy
max_velocity: 300  
max_accel: 3000    			#Max 4000
max_z_velocity: 15 			#Max 15 for 12V TMC Drivers, can increase for 24V
max_z_accel: 350
square_corner_velocity: 5.0

[temperature_sensor MCU]
sensor_type: temperature_mcu

[temperature_sensor SoC]
sensor_type: temperature_host

#####################################################################
# 	X/Y Stepper Settings
#####################################################################

## X Stepper on Motor1(B Motor)
[stepper_x]
step_pin: PE6
dir_pin: PE5
enable_pin: !PC14
microsteps: 16
rotation_distance: 40
full_steps_per_rotation:200  #set to 400 for 0.9 degree stepper
endstop_pin: ^PF4
position_min: 0
##--------------------------------------------------------------------

##	Uncomment below for 250mm build
#position_endstop: 250
#position_max: 250

##	Uncomment for 300mm build
#position_endstop: 300
#position_max: 300

##	Uncomment for 350mm build
#position_endstop: 350
#position_max: 350

##--------------------------------------------------------------------
homing_speed: 25   #Max 100
homing_retract_dist: 5
homing_positive_dir: true

##	Make sure to update below for your relevant driver (2208 or 2209)
[tmc2209 stepper_x]
uart_pin: PC13
interpolate: True
run_current: 0.8
sense_resistor: 0.110
stealthchop_threshold: 0

## Y Stepper on Motor2 (A Motor)
[stepper_y]
step_pin: PE2
dir_pin: PE1
enable_pin: !PE4
microsteps: 16
rotation_distance: 40
endstop_pin: ^PF3
full_steps_per_rotation:200  #set to 400 for 0.9 degree stepper
position_min: 0
##--------------------------------------------------------------------

##	Uncomment for 250mm build
#position_endstop: 250
#position_max: 250

##	Uncomment for 300mm build
#position_endstop: 300
#position_max: 300

##	Uncomment for 350mm build
#position_endstop: 350
#position_max: 350

##--------------------------------------------------------------------
homing_speed: 25  #Max 100
homing_retract_dist: 5
homing_positive_dir: true

##	Make sure to update below for your relevant driver (2208 or 2209)
[tmc2209 stepper_y]
uart_pin: PE3
interpolate: True
run_current: 0.8
sense_resistor: 0.110
stealthchop_threshold: 0

#####################################################################
# 	Z Stepper Settings
#####################################################################

## Z0 Stepper - Front Left on MOTOR3_A
[stepper_z]
step_pin: PB8
dir_pin: PB7
enable_pin: !PE0
rotation_distance: 40
gear_ratio: 80:16
microsteps: 16
endstop_pin: ^PF2
##  Z-position of nozzle (in mm) to z-endstop trigger point relative to print surface (Z0)
##  (+) value = endstop above Z0, (-) value = endstop below
##	Increasing position_endstop brings nozzle closer to the bed
##  After you run Z_ENDSTOP_CALIBRATE, position_endstop will be stored at the very end of your config
#position_endstop: -0.5
##--------------------------------------------------------------------

##	Uncomment below for 250mm build
#position_max: 240

##	Uncomment below for 300mm build
#position_max: 290

##	Uncomment below for 350mm build
#position_max: 340

##--------------------------------------------------------------------
position_min: -5
homing_speed: 8
second_homing_speed: 3
homing_retract_dist: 3

##	Make sure to update below for your relevant driver (2208 or 2209)
[tmc2209 stepper_z]
uart_pin: PB9
interpolate: true
run_current: 0.8
sense_resistor: 0.110
stealthchop_threshold: 0

##	Z1 Stepper - Rear Left on Motor5
[stepper_z1]
step_pin: PG13
dir_pin: !PG12
enable_pin: !PG15
rotation_distance: 40
gear_ratio: 80:16
microsteps: 16

##	Make sure to update below for your relevant driver (2208 or 2209)
[tmc2209 stepper_z1]
uart_pin: PG14
interpolate: true
run_current: 0.8
sense_resistor: 0.110
stealthchop_threshold: 0

##	Z2 Stepper - Rear Right on Motor6
[stepper_z2]
step_pin: PG9
dir_pin: PD7
enable_pin: !PG11
rotation_distance: 40
gear_ratio: 80:16
microsteps: 16

##	Make sure to update below for your relevant driver (2208 or 2209)
[tmc2209 stepper_z2]
uart_pin: PG10
interpolate: true
run_current: 0.8
sense_resistor: 0.110
stealthchop_threshold: 0

##	Z3 Stepper - Front Right on Motor7
[stepper_z3]
step_pin: PD4
dir_pin: !PD3
enable_pin: !PD6
rotation_distance: 40
gear_ratio: 80:16
microsteps: 16

##	Make sure to update below for your relevant driver (2208 or 2209)
[tmc2209 stepper_z3]
uart_pin: PD5
interpolate: true
run_current: 0.8
sense_resistor: 0.110
stealthchop_threshold: 0

#####################################################################
# 	Extruder
#####################################################################

#	E0 on Motor8
[extruder]
step_pin: PC7
dir_pin: PC8
enable_pin: !PD2
##  Update value below when you perform extruder calibration
##  If you ask for 100mm of filament, but in reality it is 98mm:
##  rotation_distance = <previous_rotation_distance> * <actual_extrude_distance> / 100
##  22.6789511 is a good starting point
rotation_distance: 22.6789511   #Bondtech 5mm Drive Gears
##  Update Gear Ratio depending on your Extruder Type
##  Use 50:10 for Stealthburner/Clockwork 2
##  Use 50:17 for Afterburner/Clockwork (BMG Gear Ratio)
##  Use 80:20 for M4, M3.1
gear_ratio: 50:10
microsteps: 16
full_steps_per_rotation: 200	#200 for 1.8 degree, 400 for 0.9 degree
nozzle_diameter: 0.400
filament_diameter: 1.75
heater_pin: PA0
##	Validate the following thermistor type to make sure it is correct

## Check what thermistor type you have. See https://www.klipper3d.org/Config_Reference.html#common-thermistors for common thermistor types.
## Use "Generic 3950" for NTC 100k 3950 thermistors
#sensor_type:

sensor_pin: PB0
min_temp: 10
max_temp: 270
max_power: 1.0
min_extrude_temp: 170
control = pid
pid_kp = 26.213
pid_ki = 1.304
pid_kd = 131.721
##	Try to keep pressure_advance below 1.0
#pressure_advance: 0.05
##	Default is 0.040, leave stock
#pressure_advance_smooth_time: 0.040

##	E0 on Motor7
##	Make sure to update below for your relevant driver (2208 or 2209)
[tmc2209 extruder]
uart_pin: PC6
interpolate: false
run_current: 0.5
sense_resistor: 0.110
stealthchop_threshold: 0

#[filament_switch_sensor material_0]
#switch_pin: PC1

#[filament_switch_sensor material_1]
#switch_pin: PC2

#####################################################################
# 	Bed Heater
#####################################################################

[heater_bed]
##	SSR Pin - HE1
heater_pin: PA1
## Check what thermistor type you have. See https://www.klipper3d.org/Config_Reference.html#common-thermistors for common thermistor types.
## Use "Generic 3950" for NTC 100k 3950 thermistors
#sensor_type:
sensor_pin: PB1
##  Adjust max_power so it doesn't exceed the SSR rating. The Omron G3NA-210B-DC5 SSR is rated at 4 amps without a heatsink.
##  The formula is "4 / (Wattage_of_bed_heater / Mains_voltage) = max_power"
##  If max_power is greater than 1.0, use 1.0
max_power: 0.6
min_temp: 0
max_temp: 120
control: pid
pid_kp: 58.437
pid_ki: 2.347
pid_kd: 363.769

#####################################################################
# 	Probe
#####################################################################

[probe]
##	Inductive Probe
##	This probe is not used for Z height, only Quad Gantry Leveling
##  NPN and PNP proximity switch types can be set by jumper
pin: PF1 #M4-STOP
x_offset: 0
y_offset: 25.0
z_offset: 0
speed: 10.0
samples: 3
samples_result: median
sample_retract_dist: 3.0
samples_tolerance: 0.006
samples_tolerance_retries: 3

#####################################################################
# 	Fan Control
#####################################################################

[fan]
##	Print Cooling Fan - CNC_FAN0
pin: PF7
kick_start_time: 0.5
##	Depending on your fan, you may need to increase this value
##	if your fan will not start. Can change cycle_time (increase)
##	if your fan is not able to slow down effectively
off_below: 0.10

[heater_fan hotend_fan]
##	Hotend Fan - CNC_FAN1
pin: PF9
max_power: 1.0
kick_start_time: 0.5
heater: extruder
heater_temp: 50.0
##	If you are experiencing back flow, you can reduce fan_speed
#fan_speed: 1.0

[heater_fan controller_fan]
##	Controller fan - CNC_FAN2
pin: PF6
kick_start_time: 0.5
heater: heater_bed
heater_temp: 45.0
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

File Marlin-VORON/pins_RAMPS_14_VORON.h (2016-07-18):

/**
 * Marlin 3D Printer Firmware
 * Copyright (C) 2016 MarlinFirmware [https://github.com/MarlinFirmware/Marlin]
 *
 * Based on Sprinter and grbl.
 * Copyright (C) 2011 Camiel Gubbels / Erik van der Zalm
 *
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
 */

/**
 * Arduino Mega with RAMPS v1.4 pin assignments
 *
 *  RAMPS_14_VORON (VORON pin config for RAMPs 1.4)
 */

// Include the base configuration for RAMPs 1.4
#include "pins_RAMPS_14.h"

#define CONTROLLERFAN_PIN  8 // D8 on RAMPs. Used for the fan to cool controller 
 							 // LED strip can be attached to the same output. This way LEDs are only on during printing, and shortly after

// Fan Expansion board pins
#define EXTRUDER_0_AUTO_FAN_PIN 6 // Servo pin 6 for E3D Fan
#define EXTRUDER_1_AUTO_FAN_PIN 6 // Servo pin 6 for E3D Fan (same pin for both extruders since it's the same fan)

#define FAN_PIN            		5 // Servo pin 5 for parts cooling pan

// Extruders
#define HEATER_0_PIN     10   // D10 on RAMPs. Extruder 1
#define HEATER_1_PIN     9    // D9 on RAMPs.  Extruder 2

#define TEMP_0_PIN       13   // T0 on RAMPs
#define TEMP_1_PIN       15   // T2 on RAMPs

// Bed
#define HEATER_BED_PIN   11   // Servo pin 11 to drive the SSR
#define TEMP_BED_PIN     14   // T1 on RAMPs

// LCD
#define BEEPER_PIN 		 -1   // Disable Beeper Pin

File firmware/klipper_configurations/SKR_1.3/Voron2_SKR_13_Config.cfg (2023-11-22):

## Voron Design VORON2 250/300/350mm SKR 1.3 TMC2209 UART config

## *** THINGS TO CHANGE/CHECK: ***
## MCU paths                            [mcu] section
## Thermistor types                     [extruder] and [heater_bed] sections - See https://www.klipper3d.org/Config_Reference.html#common-thermistors for common thermistor types
## Z Endstop Switch location            [safe_z_home] section
## Homing end position                  [gcode_macro G32] section
## Z Endstop Switch  offset for Z0      [stepper_z] section
## Probe points                         [quad_gantry_level] section
## Min & Max gantry corner postions     [quad_gantry_level] section
## PID tune                             [extruder] and [heater_bed] sections
## Fine tune E steps                    [extruder] section

##========================== Pin Definitions ========================
## X_STEP_PIN         2.2
## X_DIR_PIN          2.6
## X_ENABLE_PIN       2.1
## X_MIN_PIN          1.29
## X_MAX_PIN          1.28
## X_UART_RX          1.17
## X_UART_TX          4.29

## Y_STEP_PIN         0.19
## Y_DIR_PIN          0.20
## Y_ENABLE_PIN       2.8
## Y_MIN_PIN          1.27
## Y_MAX_PIN          1.26
## Y_UART_RX          1.15
## Y_UART_TX          1.16

## Z_STEP_PIN         0.22
## Z_DIR_PIN          2.11
## Z_ENABLE_PIN       0.21
## Z_MIN_PIN          1.25
## Z_MAX_PIN          1.24
## Z_UART_RX          1.10
## Z_UART_TX          1.14

## E0_STEP_PIN        2.13
## E0_DIR_PIN         0.11
## E0_ENABLE_PIN      2.12
## E0_UART_RX         1.8
## E0_UART_TX         1.9

## E1_STEP_PIN        0.1
## E1_DIR_PIN         0.0
## E1_ENABLE_PIN      0.10
## E1_UART_RX         1.1
## E1_UART_TX         1.4

## HE1                2.4    
## HE0                2.7
## BED                2.5
## TH1 (H1 Temp)      0.25
## TH0 (H0 Temp)      0.24
## TB  (Bed Temp)     0.23
## FAN                2.3
## SERVO              2.0
##===================================================================

##  MCU for X/Y/E steppers main MCU
##  [X in X] - B Motor
##  [Y in Y] - A Motor
##  [E in E0] - Extruder
[mcu]
##  Obtain definition by "ls -l /dev/serial/by-id/" then unplug to verify
##--------------------------------------------------------------------
serial: /dev/serial/by-id/usb-Klipper_lpc1768_00000-if00
##--------------------------------------------------------------------

##  MCU for Z steppers
##  [Z in X] - Front Left
##  [Z1 in Y] - Rear Left
##  [Z2 in Z] - Rear Right
##  [Z3 in E0]- Front Right
[mcu z]
##  Obtain definition by "ls -l /dev/serial/by-id/" then unplug to verify
##--------------------------------------------------------------------
serial: /dev/serial/by-id/usb-Klipper_lpc1768_00000-if00
##--------------------------------------------------------------------

[printer]
kinematics: corexy
max_velocity: 300  
max_accel: 3000             #Max 4000
max_z_velocity: 15          #Max 15 for 12V TMC Drivers, can increase for 24V
max_z_accel: 350
square_corner_velocity: 5.0

#####################################################################
#   X/Y Stepper Settings
#####################################################################

##  Connected to X on mcu_xye (B Motor)
[stepper_x]
step_pin: P2.2
dir_pin: !P2.6
enable_pin: !P2.1
rotation_distance: 40
microsteps: 32
full_steps_per_rotation:200  #set to 400 for 0.9 degree stepper
endstop_pin: P1.28
position_min: 0
##--------------------------------------------------------------------

##  Uncomment below for 250mm build
#position_endstop: 250
#position_max: 250

##  Uncomment for 300mm build
#position_endstop: 300
#position_max: 300

##  Uncomment for 350mm build
#position_endstop: 350
#position_max: 350

##--------------------------------------------------------------------
homing_speed: 25   #Max 100
homing_retract_dist: 5
homing_positive_dir: true

##  Make sure to update below for your relevant driver (2208 or 2209)
[tmc2209 stepper_x]
uart_pin: P1.17
interpolate: False
run_current: 0.8
sense_resistor: 0.110
stealthchop_threshold: 0

##  Connected to Y on mcu_xye (A Motor)
[stepper_y]
step_pin: P0.19
dir_pin: !P0.20
enable_pin: !P2.8
rotation_distance: 40
microsteps: 32
full_steps_per_rotation:200  #set to 400 for 0.9 degree stepper
endstop_pin: P1.26
position_min: 0
##--------------------------------------------------------------------

##  Uncomment for 250mm build
#position_endstop: 250
#position_max: 250

##  Uncomment for 300mm build
#position_endstop: 300
#position_max: 300

##  Uncomment for 350mm build
#position_endstop: 350
#position_max: 350

##--------------------------------------------------------------------
homing_speed: 25  #Max 100
homing_retract_dist: 5
homing_positive_dir: true

##  Make sure to update below for your relevant driver (2208 or 2209)
[tmc2209 stepper_y]
uart_pin: P1.15
interpolate: False
run_current: 0.8
sense_resistor: 0.110
stealthchop_threshold: 0
 
#####################################################################
#   Z Stepper Settings
#####################################################################

## Z MCU - In X Position
## Z0 Stepper - Front Left
[stepper_z]
step_pin: z:P2.2
dir_pin: !z:P2.6
enable_pin: !z:P2.1
rotation_distance: 40
gear_ratio: 80:16
microsteps: 32
endstop_pin: z:P1.25
##  Z-position of nozzle (in mm) to z-endstop trigger point relative to print surface (Z0)
##  (+) value = endstop above Z0, (-) value = endstop below
##  Increasing position_endstop brings nozzle closer to the bed
##  After you run Z_ENDSTOP_CALIBRATE, position_endstop will be stored at the very end of your config
position_endstop: -0.5
##--------------------------------------------------------------------

##  Uncomment below for 250mm build
#position_max: 210

##  Uncomment below for 300mm build
#position_max: 260

##  Uncomment below for 350mm build
#position_max: 310

##--------------------------------------------------------------------
position_min: -5
homing_speed: 8
second_homing_speed: 3
homing_retract_dist: 3

##  Make sure to update below for your relevant driver (2208 or 2209)
[tmc2209 stepper_z]
uart_pin: z:P1.17
interpolate: False
run_current: 0.8
sense_resistor: 0.110
stealthchop_threshold: 0

##  Z MCU - In Y Position
##  Z1 Stepper - Rear Left
[stepper_z1]
step_pin: z:P0.19
dir_pin: z:P0.20
enable_pin: !z:P2.8
rotation_distance: 40
gear_ratio: 80:16
microsteps: 32

##  Make sure to update below for your relevant driver (2208 or 2209)
[tmc2209 stepper_z1]
uart_pin: z:P1.15
interpolate: False
run_current: 0.8
sense_resistor: 0.110
stealthchop_threshold: 0

##  Z MCU - In Z Position
##  Z2 Stepper - Rear Right
[stepper_z2]
step_pin: z:P0.22
dir_pin: !z:P2.11
enable_pin: !z:P0.21
rotation_distance: 40
gear_ratio: 80:16
microsteps: 32

##  Make sure to update below for your relevant driver (2208 or 2209)
[tmc2209 stepper_z2]
uart_pin: z:P1.10
interpolate: False
run_current: 0.8
sense_resistor: 0.110
stealthchop_threshold: 0

##  Z MCU - In E0 Position
##  Z3 Stepper - Front Right
[stepper_z3]
step_pin: z:P2.13
dir_pin: z:P0.11
enable_pin: !z:P2.12
rotation_distance: 40
gear_ratio: 80:16
microsteps: 32

##  Make sure to update below for your relevant driver (2208 or 2209)
[tmc2209 stepper_z3]
uart_pin: z:P1.8
interpolate: False
run_current: 0.8
sense_resistor: 0.110
stealthchop_threshold: 0


#####################################################################
#   Extruder
#####################################################################

#   E0 on MCU X/Y
[extruder]
step_pin: P2.13
dir_pin: P0.11
enable_pin: !P2.12
##  Update value below when you perform extruder calibration
##  If you ask for 100mm of filament, but in reality it is 98mm:
##  rotation_distance = <previous_rotation_distance> * <actual_extrude_distance> / 100
##  22.6789511 is a good starting point
rotation_distance: 22.6789511   #Bondtech 5mm Drive Gears
##  Update Gear Ratio depending on your Extruder Type
##  Use 50:10 for Stealthburner/Clockwork 2
##  Use 50:17 for Afterburner/Clockwork (BMG Gear Ratio)
##  Use 80:20 for M4, M3.1
gear_ratio: 50:10
microsteps: 32
full_steps_per_rotation: 200    #200 for 1.8 degree, 400 for 0.9 degree
nozzle_diameter: 0.400
filament_diameter: 1.75
heater_pin: P2.7
## Check what thermistor type you have. See https://www.klipper3d.org/Config_Reference.html#common-thermistors for common thermistor types.
## Use "Generic 3950" for NTC 100k 3950 thermistors
#sensor_type:
sensor_pin: P0.24
min_temp: 10
max_temp: 270
max_power: 1.0
min_extrude_temp: 170
control = pid
pid_kp = 26.213
pid_ki = 1.304
pid_kd = 131.721
##  Try to keep pressure_advance below 1.0
#pressure_advance: 0.05
##  Default is 0.040, leave stock
#pressure_advance_smooth_time: 0.040

##  E0 on MCU X/Y
##  Make sure to update below for your relevant driver (2208 or 2209)
[tmc2209 extruder]
uart_pin: P1.9
interpolate: false
run_current: 0.5
sense_resistor: 0.110
stealthchop_threshold: 0
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

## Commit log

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2015-12-07 Tons of changes, most didn't work out. oh well
    [Configuration.h, Configuration_adv.h]
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2016-03-25 Moving old stuff to Old to avoid confusion
    [Carriage End A.stl, Carriage End B.stl, Harness Anchor.stl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]
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2016-06-07 CLEAN ALL THE THINGS. Fixes #30, Fixes #23
    [Bed Support Carriage (TR8 Nut).stl, Carriage End A.stl, Carriage End B.stl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]
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2016-06-10 Beefing up Z probe mount. Wire management. Fixes #34
    [carriage_end_a.stl, carriage_end_b.stl, wire_harness_clip.stl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]
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2016-06-10 Fixing the comment for the bed temp pin
    [pins_RAMPS_14_VORON.h]
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2016-06-26 Tweak to 1.75mm version to prevent PTFE kinking out Also, 13mm TR8 nut version of the bed carriage mid.
    [bed_carriage_midsection_13mm_nut.stl, main_body_1.75mm.stl]
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2016-12-28 Finalized 1.5 gantry parts. Fixed a few issues reported on reddit
    [a_idler_lower.stl, a_idler_upper.stl, a_motor_mount.stl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]
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2018-01-31 Add Filtered Mains Inlet, Duet Brackets and Alternate PSU Brackets for LSU-200-24 or similar (#116)
    * Add Filtered Mains Inlet
    * add alternate PSU Bracket and Duet Brackets
    add alternate PSU Bracket and Duet Brackets
    * update model orientation
    * M3 Hardware instead of M5
    * fix corrupted stls
    [2020 Offset Extrusion Support.STL, Alternate PSU Bracket - LRS-200-24 x2.STL, Duet Bracket - From 2020 Extrusion x4 (Use Metal Standoffs or Plastic Spacers).ST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]
2018-01-31 Typo: Stabalizer -> Stabilizer (#110)
    Fixed a typo in STLs/VORON2/Front Idlers/front_idler_stabilizer_x2.stl
    Courtesy of @ampex V022
    [front_idler_stabilizer_x2.stl]
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2018-02-11 AB Drive rework. Mobius mount and inlet for bowden. Z rail stops.
    [a_drive_module_lower.stl, a_drive_module_upper.stl, b_drive_module_lower.stl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]
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2018-02-25 Adding configuration files to support both 1.1.6 and 1.1.8 (#120)
    * Adding configuration files to support both 1.1.6 and 1.1.8
    I've done my best to clean printer-specific configuration from the files, this should work with most default VORONs. Someone should come in behind me and double check my work though.
    * Minor changes to UBL probing offsets to account for Chimera offset, disabled software endstops to match original voron config.
    * Removing 1.1.6, responding to review comments.
    * Adding methods that I missed to ultralcd.
    [Configuration.h]
2018-02-25 update IR sensor bracket (#118)
    * update ir bracket with vent holes
    * add step for 40mm fan with new IR bracket
    * add 120mm fan filter and cover
    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
    [Inductive_Sensor_Mount_Off_Fan_Bracket.STL, filter_cover_120mm.STL, filter_fan_mount_120mm.STL]
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2018-03-09 daveidmx's Duet config (250mm, 0.9°) (#125)
    * Adding baseline Duet config.
    * * Fix heater parameters to use the full model, rather than simplified PID.
    * Up the accelerations a bit.
    [bed.g, config.g, homeall.g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]
2018-03-12 Squashed commit of the following: (#126)
    commit 2fd9c11ec0e14efc2361e74de33b0ee0eced168b
    Author: David Govek <daveidmx@gmail.com>
    Date: Sun Mar 11 22:06:23 2018 -0700
    Ease off on retraction.
    commit b276bf6ef48ead15938f9146370a6dea05491631
    Author: David Govek <daveidmx@gmail.com>
    Date: Sun Mar 11 22:04:15 2018 -0700
    Duet 1.21 compatibility, features, and some cleanup.
    * Use "S2" moves during homing.
    * Enable multi-tap Z-probing.
    * Add sensor recovery time "R0.1" to cover the input stability hiccup during probe switch transitions.
    * Move the fast inductive Z-plunge from the center to the corner of the bed so if the nozzle impacts it's less damaging.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
    [bed.g, config.g, homex.g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]
2018-04-20 daveidmx config refactor, documentation, and mechanical test scripts (#131)
    * First round tuning
    * Config tuning for heaters, fans, and temp inductive Z probe.
    * Tuning for Z probe nozzle switch
    * Z level
    * Inductive probe speed change to be slower
    * Making Z probes two-pass fast-slow. Adding macros for configuring Z probes.
    * Run bed leveling twice.
    Make fast probe configs have Z0.
    Tweak slow mechanical Z offset.
    * Tuning firmware retraction.
    * COntinuing to tweak leveling and speeds.
    * Slowing down acceleration.
    * Add comments on motor locations
    * Add comment re M587
    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
    [01_home_z_mech.g, 01_physics_z_100.g, 01_physics_z_1000.g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]
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2018-05-25 Add PanelDue7 TS, reorganize volcom mods folder (#134)
    * add paneldue7 ts, and reorganize folder
    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
    [40mm fan duct.STL, 40mm_Fan_Duct.STL, 40x40x10mm_Fan_Duct.STL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]
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2018-06-17 Config updates to support RRF 2.0/DWC, plus miscelaneous fixes and improvements (#137)
    * Remove comment with sample temperature from filament_do_moves_for_unload.g. I don't want to give advice because I don't really trust this script.
    * Increase PLA unload temperature.
    * Add a third bed leveling pass. It's usually not necessary, but if your gantry is out of whack or your measurements aren't dialed in it can help.
    * Updating E3D thermistor config as per https://wiki.e3d-online.com/E3D-v6_Assembly#Configure_Firmware_.28Easy.21.29
    * Increasing motor idle timeout. When the Z current goes idle, the Z drives can drop a step resulting in a slight gantry tilt. Increasing to 1 hour so tha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
    [01_home_z_mech.g, 01_physics_z_100.g, 01_physics_z_1000.g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]
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2018-09-25 Squashed commit of the following: (#149)
    commit 4571634a244e5912208fa9b78c50bdbd1f531b5f
    Date: Wed Sep 19 22:20:33 2018 -0700
    Fix incorrect tool heater macro invocation.
    commit d6cf1dc97b39546301e76b74bcad7d17448eb26e
    Date: Wed Sep 19 22:19:48 2018 -0700
    README.txt
    commit 1ca53703f9bfd353c0dcf8468625f90d832aad3a
    Date: Wed Sep 19 22:19:32 2018 -0700
    Genericizing for public consumption.
    commit bf13241284b916abe292e3657964aca2f6917564
    Date: Wed Sep 19 21:17:39 2018 -0700
    Initial co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
    [01_physics_z_100.g, 01_physics_z_1000.g, 02_physics_xy_1.g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]
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2018-10-01 daveidmx V2.1 config features and fixes (#150)
    * Increase idle timeout to 24 hours, and set motors to turn off.
    * Set electronics fan min PWM and blip time because my fans are sluggish.
    * Extruder drive current adjustments based on PA trials to avoid skipping steps.
    * Preheat scripts used the wrong fan control command. And fix some temps.
    * Make toolhead heater selection sticky by writing out /sys/restore_tool_heater.g.
    * Reduce default PLA print temp.
    * Make firmware retraction profile selection sticky by writing out to /sys/restore_retraction.g.
    Make separate profiles for V6 and Volcano.
    * Filament sensors need to be _turned on_.
    * Release notes.
    [config.g, e_fullcurrent.g, pa_nozhop.g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]
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2018-11-09 daveidmx duet config updates (#159)
    * Pulling in comments from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
    [calibrate_mswitch.g, center_xyz.g, coarse_level.g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]
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2018-12-05 Add 1/8 in panel clips (#172)
    * Add 1/4in panel clips
    * fix readme
    [corner_panel_clip_0.125in_version_x12.stl]
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2018-12-05 Mods for LED bars and Einsy Rambo (#175)
    * Mods
    * Fixed incorrect Link Syntax
    * added Einsy config to main config folder
    * documented inverted enable-pins
    * added pictures
    [Anet_12864_front.stl, Anet_12864_rear.stl, cable_cover v9.step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]
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2018-12-29 Adding missing motor covers, cleanup (#183)
    * Cleanup for the V1.6 release
    * Updating the readme
    * Adding missing motor covers, cleanup
    [01_physics_z_100.g, 01_physics_z_1000.g, 02_physics_xy_1.g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]
2018-12-29 Revert " Adding missing motor covers, cleanup (#183)"
    This reverts commit 24c323d0988ad0e75a9b7b03d6dd1cf20c111311.
    [01_physics_z_100.g, 01_physics_z_1000.g, 02_physics_xy_1.g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]
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2019-01-26 daveidmx config: FSR, leave heating on, move to Duet folder (#181)
    * Release notes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
    [01_physics_z_100.g, 01_physics_z_1000.g, 02_physics_xy_1.g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]
2019-01-26 Add files via upload (#184)
    * Update VORON2_stock_250_printer.cfg
    added extra text at the top of the file and removed a couple of macros to keep it as simple and avoid any confusion for new users
    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
    [VORON2_stock_250_printer.cfg]
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2019-03-15 Update Profiles, Remove Broken PanelDue Assembly Mod
    Panel Due never worked right, update slic3r settings
    [PanelDue7 Front.STL]
2019-04-08 add 2.1.1 parts
    fix clearances in front idlers, add electronics brackets, add filtered power inlet, add new 80t
    [_vlock_a.stl, _vlock_b.stl, _vlock_ring_80t.stl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]
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2019-04-13 extra clearance to cable cover for 20mm tape chain bridge
    extra clearance to cable cover for 20mm tape chain bridge
    [cable_cover_left.stl, cable_cover_right.stl]
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2019-05-23 added mzbot cube and 3 test prints
    if you can print these and they thread together/look good with no issues, you can print a voron
    [MZBOT_Cube.stl, Thread Test 1.STL, Thread Test 2.STL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]
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2019-06-27 Updated VORON2_stock_250_printer.cfg
    ~Updated stock config file to include new sections and parameters from Klipper changes.
    ~Removed an M104 S0 line from PRINT_START which caused errors on some slicers.
    ~Lowered initial accel and velocity values to encourage users to do their own testing and tweaking to their specific machine.
    ~Added some notes on several variables to help alleviate confusion.
    ~This config was uses as a baseline for harmonizing and standardizing stock config files for 250/300/250 machines.
    [VORON2_stock_250_printer.cfg]
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2019-06-29 6mm Panel locks & C920 webcam mount (#21)
    * Add additional mods and add naming consistency
    6mm Glass lock mod
    C920 Webcam mount
    Fix extension of readme so it renders correctly.
    Edit readme with assembly for webcam
    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
    [C920_Top_Front_Mount.step, C920_Top_Front_Mount.stl, Lock_Body.step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]
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2019-07-17 reinforce duet and skr mounting bracket
    reinforce duet and skr mounting bracket
    [bigtree_skr_single_board_mounting_frame_x2.STL, duet_duex_single_board_mounting_frame_x2.STL]
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2019-08-10 mods: added missing hall magnet slot back to remodeled x carriage right frame
    [x_carriage_frame_right_remodeled.stl]
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2019-09-10 Update VORON2_stock_300_printer.cfg
    Fixing G32 to do one quad and home z afterwards (unifying to stock 250 config)
    [VORON2_stock_300_printer.cfg]
2019-09-10 Update VORON2_stock_350_printer.cfg
    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
    [VORON2_stock_350_printer.cfg]
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2019-10-19 README.md files from mods folder and klipper configuration link fixes (#46)
    * fixes and changes to md files to use relative linking
    * Fixed for the change to Voron 2 to be valid
    * Fixed for the change to point to Mobius and be proper md file
    * Fixed link
    * Fixed configurations only for links
    * Removed double parenthesis
    [VORON2_stock_250_printer.cfg, VORON2_stock_300_printer.cfg, VORON2_stock_350_printer.cfg]
2019-10-20 Add files via upload (#42)
    Added 2-to-1 Adapter mount to mods/Danowar
    Added dual Mobius mount to mods/Danowar
    * Moved Folder
    Moved folder to correct location
    * Chnged Folder names to remove spaces
    * Added Humidity Sensor Bracket
    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
    [Bracket.stl, Dual Mobuis Mount.stl, Humidity Sensor Bracket.f3d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]
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2019-11-01 Many Small Updates and QOL items
    Update Bottom DXF, add 80mm Bottom and Back Fan Mounts (back requires cutting of charcoal filter), Pi Bracket for Pi with Heatsink Case, Short Nozzle Scrubber Holder, Skirts that take less material, re-add cable anchors for gantry
    [Bottom Panel - 200^3.DXF, Bottom_Panel-250^3.DXF, Bottom_Panel-300^3.DXF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]
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2019-11-03 Add direct drive mod for 2.1/2.2 (#51)
    * Direct drive mod for 2.1 and 2.2.
    * Add example image to direct drive mod readme.md
    * Add assembly instructions to direct drive mod readme.md
    * Fix m2.5-m2 assembly instructions bug in direct drive mod readme.md
    * Add v6 direct drive mount.
    E3d v6 is reported to be 1.1mm taller than the mosquito all mounted up.
    This change should retain the nozzle elevation to help keep inductive
    probes working if someone mounts a v6 to the BMG mount plate.
    * direct drive model improvements
    * make room for extra belt
    * add 0.32mm seats for back side nuts
    * Fix support arm model bug in v6
    * drop the fan nozzle outlet as low as I dare
    * ad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
    [a_corner_tube.stl, a_corner_wire_guide.stl, fan_mount.stl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]
2019-11-03 Update Klipper config files (#56)
    * printer busy checks for macros
    adds safeguards to macros that will interrupt a print
    * printer busy checks for macros - 300mm
    * printer busy checks for macros - 350
    * updated config descriptions
    * style harmonization
    * fix z min switch pos
    [VORON2_stock_250_printer.cfg, VORON2_stock_300_printer.cfg, VORON2_stock_350_printer.cfg]
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2019-11-04 Revert "Add direct drive mod for 2.1/2.2 (#51)" (#58)
    This reverts commit 738d83cce128ebcdb36d22b7013ed0611371e041.
    [a_corner_tube.stl, a_corner_wire_guide.stl, fan_mount.stl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]
2019-11-04 Adjust Z Tensioner Travel
    it was possible to overextend the Z belt tensioners, such that they would actually rotate out, this corrects that issue
    [9mm_z_idler_frame_mirror_x2_Rev1.stl, 9mm_z_idler_frame_mirror_x2_Rev2.stl, 9mm_z_idler_frame_x2_Rev1.STL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]
2019-11-05 [quad_gantry_level] fix typos in 300 & 350 config comments (#57)
    * Updated [quad_gantry_level] typo
    Changed MAX (250,250) to MAX (300,300)
    * Updated [quad_gantry_level] typo
    Changed MAX (250,250) to MAX (350,350)
    [VORON2_stock_300_printer.cfg, VORON2_stock_350_printer.cfg]
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2019-11-06 Klipper configs - lower max_z_accel, default square_corner_velocity (#63)
    * lowered z_accel, lowered square_corner_volocity
    - Reduce z accel to safer values for 250 & 300mm configs.
    - lowered square_corner_velocity to the default value of 5
    * updated comments
    - FSR was replaces by z switch
    - removed extraneous line
    [VORON2_stock_250_printer.cfg, VORON2_stock_300_printer.cfg, VORON2_stock_350_printer.cfg]
2019-11-06 Repair STL issues with XY Bridge and Idler Frame, side skirts were 1mm short (#61)
    * fix inverted mirror idler frame
    * fix unprintable overhang - v21 xy bridge
    * fix unprintable overhang - v2.2 xy bridge
    * side skirts were 1mm short compared to front
    [9mm_z_idler_frame_mirror_x2_Rev2.stl, 9mm_z_idler_frame_mirror_x2_Rev3.stl, front_rear_skirt_b_150spec_x1_Rev2.STL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]
2019-11-07 Re-add BMG mod for 2.1 / 2.2 (#62)
    * add kn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
    [fan_mount.step, fan_mount.stl, gumby_mount_mosquito.step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]
2019-11-09 replace x carriage 2.1 mount with one that works, add chamfer to bottom of blanking plate (#66)
    [front_blank_skirt_panel_200spec_to_350spec_only_x1_Rev1.stl, front_blank_skirt_panel_200spec_to_350spec_only_x1_Rev2.stl, x_carriage_frame_zipchain_bar_+20mm_x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]
2019-11-11 Swap XY Bridge +20mm parts between 2.1 and 2.2 to resolve issue #70
    [v21_xy_bridge_+20mm_x1_Rev2.STL, xy_bridge_+20mm_x1_Rev2.STL]
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2019-11-15 Apply changes to master to Voron2.2 branch (#76)
    * clean up firmware directory (#74)
    * Remove mods from Voron-2 repository (#75)
    * Remove outdated slicer profiles, fix klipper readme (#73)
    [VORON2_stock_250_printer.cfg, VORON2_stock_300_printer.cfg, VORON2_stock_350_printer.cfg]
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2020-04-23 Adding universal Z chain mount, fixing front idlers, fixing and renaming brackets
    [[a]_z_chain_retainer_bracket_x2.stl, a_drive_frame_lower.stl, a_drive_frame_upper.stl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]
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2020-04-30 V2.4 clockwork ocd cleanup (#124)
    * Re-fixing interference issues with the blower fan
    * front and rear bearing holes are now the same size, plus some cleanup
    [extruder_body.stl, extruder_motor_plate.stl]
2020-05-04 V2.4 patch6 (#126)
    * Fixing clearances and adding alignment features
    * Fixing major interference issue with Y chain mount, renaming chain mounts to align with configurator terminology
    [[a]_xy_joint_cable_bridge_befenbay.stl, [a]_xy_joint_cable_bridge_generic.stl, [a]_xy_joint_cable_bridge_igus.stl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]
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2020-07-08 Z endstop fix (#160)
    * Z endstop fix
    * Update with JST version
    [nozzle_probe.stl]
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2020-09-29 Fix setdisplayneopixel macros on SKR1.3 and 1.4 configs. (#189)
    * Fix setdisplayneopixel macro on SKR1.4 config
    * Fix setdisplayneopixel macro on SKR1.3
    [Voron2_SKR_13_Config.cfg, Voron2_SKR_14_Config.cfg]
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2020-12-09 Fix for several issues (#125) (#201) (#198)
    * Updated Z stepper mounts
    * Files repaired. Fixes issue #125
    * Revert "Files repaired. Fixes issue #125"
    This reverts commit d0c435525ba87bc1024418adbb3205bb80a6ec45.
    * Files repaired. Fixes issue #125
    * klipper config: update neopixel color_order option
    * restores working STL revision under updated name
    Issue #167 broke the STL file
    A file rename should not have added ~100KB of data and broken the STL
    for usage.
    This commit reverts the file to its previously working state under the
    new filename identified in issue #167.
    * force github actions
    * Rev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
    [Voron2_SKR_13_Config.cfg, Voron2_SKR_14_Config.cfg, [a]_60mm_fan_blank_insert_x2.stl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]
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2021-05-04 Updated AB_Drive_Units to help prevent belt routing issues. Also updated [a]_cable_cover.stl to reduce chance of breaking upon installation
    [[a]_cable_cover.stl, a_drive_frame_upper.stl, b_drive_frame_lower.stl]
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2021-05-04 Fix caselight in SKR1.4 config (#230)
    Change Caselight value from 100 -> 1
    [Voron2_SKR_14_Config.cfg]
2021-05-04 Fix caselight in SKR1.3 config (#231)
    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
    [Voron2_SKR_13_Config.cfg]
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2021-12-06 Add reference config file for BTT Octopus board (#270)
    * Add reference config file for BTT Octopus board
    * fix messing newline at end of file
    * Update config to match wiring diagrams. Update microsteps to 32. Disable interpolation.
    * fixed error caused by controller_fan config.
    * Fix suggested bed thermistor type
    * Add note about updating thermistor types for heaters.
    * Reduce max z height to avoid crashes. add pull-down resistor for Octopus Pro PROBE port
    * Comment out PA values
    * remove hold_current values, as hold_current defaults to run_current.
    * Fix capitalization.
    [Voron2_Octopus_Config.cfg]
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2021-12-30 Remove leading spaces from selectable config options that could lead to klipper errors if user is not familiar with config syntax. (#289)
    [Voron2_Octopus_Config.cfg]
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2022-02-19 Updated STLs for Voron 2.4r2 release. See release notes for detailed change log. Includes fix for issue #255
    [BIGDIPPER_bracket_set.stl, BTT_MOT_EXP_bracket.stl, Duet2_Duet3Mini5_bracket_set.stl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]
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2022-02-19 Corrected Revo Micro toolhead files to match the other toolheads naming format.
    [printhead_front_e3d_revo_micro.stl, printhead_rear_e3d_revo_micro.stl]
2022-02-19 Update retraction speeds and lengths (#283)
    * Update retraction speeds and lengths
    I changed all default lengths and speeds to both be consistent and have a short default length. Yanking it 10mm back at 60mm/s is just asking for trouble. There's been many clogs because of these defaults. This is a safe startingpoint that might be a little annoying with ooze during next print, but users can tweak this WITHOUT a clogged hotend.
    * Update to 5mm@30mm/s
    [VORON2_RAMPS_250_printer.cfg, VORON2_RAMPS_300_printer.cfg, VORON2_RAMPS_350_printer.cfg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]
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2022-03-16 Add G90 before G0 in G32 macro (#295)
    * Add G90 before G0 in G32 macro
    * Added SAVE_GCODE_STATE to G32 macro for safe G90. Moved G90 to top of G32 macro.
    * Remove BED_MESH_CLEAR from G32 to resolve conflicts.
    * Added G90 to PRINT_START macro
    [Voron2_Octopus_Config.cfg, Voron2_SKR_13_Config.cfg, Voron2_SKR_14_Config.cfg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]
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2022-07-04 Update Z max position (#352)
    * Update Z max position
    280mm is enough to crash the gantry in the top of the printer. Lowered it to 260 to prevent this.
    * Remove 20mm from 250/350 too
    [Voron2_Octopus_Config.cfg, Voron2_SKR_13_Config.cfg, Voron2_SKR_14_Config.cfg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]
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2022-09-29 Shiftingtech display order (#391)
    * Update Voron2_Octopus_Config.cfg
    swapped comments and headers in the display sections, to hopefully reduce user confusion
    style change for consistent placement of description before section header
    * Update Voron2_Octopus_Config.cfg
    further cleanups
    cleanups to the cleanups, as one does
    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
    [Voron2_Octopus_Config.cfg, Voron2_SKR_13_Config.cfg, Voron2_SKR_14_Config.cfg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]
2022-12-13 Remove unnecessary letter in config (#402)
    There is the letter "M" in line 572 which causes an error.
    [Voron2_SKR_14_Config.cfg]
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2023-03-02 Multiple discrepancies between stl and cad models of electronics bay brackets #365 (#405)
    * Update PSU_stabilizer_50mm.stl
    Updated to match current CAD
    * Removed fastener models included by mistake
    * Fixed STL orientation
    * Used high refinement in Fusion360 vs medium refinement
    [PSU_stabilizer_50mm.stl]
2023-03-02 stock config updates (#410)
    updated print end and g32 to use the printer.toolhead object so you no longer need to uncomment what size printer you are building as well as added a park macro
    updated print end and g32 to use the printer.toolhead object so you no longer need to uncomment what size printer you are building as well as added a park macro
    updated print end and g32 to use the printer.toolhead object so you no longer need to uncomment what size printer you are building as well as added a park macro
    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
    [Voron2_Octopus_Config.cfg, Voron2_SKR_13_Config.cfg, Voron2_SKR_14_Config.cfg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]
2023-03-03 Side fan angle fix, z belt cover fix (#419)
    * Delete side_fan_support_x2.stl
    * cad file upload
    * Delete z_belt_cover_a_x2.stl
    * Delete z_belt_cover_b_x2.stl
    * Delete wago_221-415_mount_3x5.stl
    * Delete side_fan_support_x2.STL
    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
    [side_fan_support_x2.STL, side_fan_support_x2.stl, wago_221-415_mount_3by5.stl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]
2023-03-03 Correct probe inversion comment (#314)
    The comment in the SKR1.4 file uses the incorrect syntax for inverting the probe connection (at least as of current klipper).
    The ! and ^ were transposed.
    [Voron2_SKR_14_Config.cfg]
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2023-09-09 Update config files to reflect SSR rating instead of the old, incorrect "warp" rating. (#448)
    Change bed_heater formula to insure max_power doesn't exceed SSR rating.
    Change bed_heater formula to insure max_power doesn't exceed SSR rating.
    Change bed_heater formula to insure max_power doesn't exceed SSR rating.
    Change bed_heater formula to insure max_power doesn't exceed SSR rating.
    Change bed_heater formula to insure max_power doesn't exceed SSR rating.
    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
    [Voron2_M8P_config.cfg, Voron2_Octopus_Config.cfg, Voron2_SKR_13_Config.cfg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]
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2023-11-22 Fix config file consistency and clarify GCode state command usage (#136) (#452)
    The PRINT_END macro in the Octopus config file contains a pair of
    SAVE_GCODE_STATE/RESTORE_GCODE_STATE command. The purpose of those
    commands is to allow the macro to perfom actions at the end of the
    print and then restore the printer state as it was prior to the
    macro's execution (restore coordinate system and speeds).
    However, there was some confusion as to the effect of those calls,
    particularly the RESTORE_GCODE_STATE. What is desired is that the
    printer state is restored but the toolhead position is not.
    To clarify the intention and prevent any issues, the "MOVE=0"
    argument to RESTORE_GCODE_STAT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
    [Voron2_M8P_config.cfg, Voron2_Octopus_Config.cfg, Voron2_SKR_13_Config.cfg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]
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2025-05-30 Bugfix: Correct dir_pin on stepper_z1 and stepper_z2 (#489)
    * Correct dir_pin on stepper_z1 and stepper_z2
    Tried moving gantry up using sample config. The front side moved up and the back side moved down.
    Checked other sample configs and found ! on dir_pin normally look similar between motors z and z2, and motors z1 and z3. Previous commit has ! on dir_pin similar between motors z and z1, and the motor z2 and z3.
    Swapping the ! on dir_pin on z1 and z2 corrects the issue
    [Voron2_M8P-v2.0_config.cfg]

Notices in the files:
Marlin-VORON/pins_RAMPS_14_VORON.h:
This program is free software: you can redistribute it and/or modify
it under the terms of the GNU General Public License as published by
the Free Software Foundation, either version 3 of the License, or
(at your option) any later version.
